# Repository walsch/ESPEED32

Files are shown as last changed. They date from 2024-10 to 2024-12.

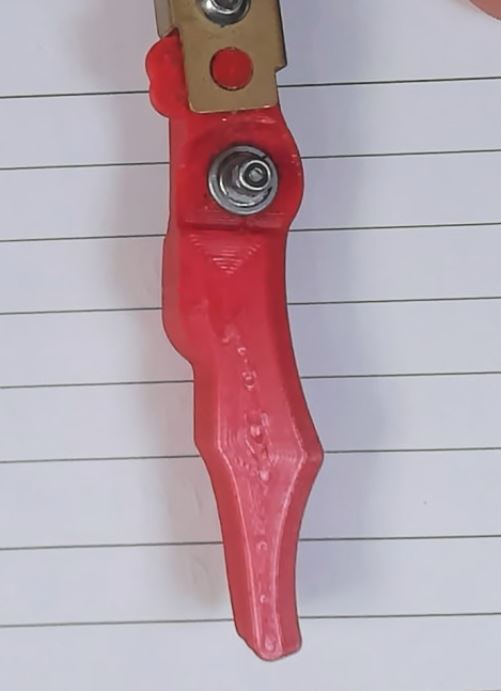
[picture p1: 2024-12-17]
Mechanical/longButton.JPG

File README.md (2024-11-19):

# SlotEsp32
WARNING: the magnetic sensor TLE493D-P3B6 A0 is the version 3 silicon and will be available on Digikey or mouser very likely in feb 2025
Cutting edge Slot car controller that has an ESP32 at its heart.
How to built it video:
https://github.com/MakerFabio/ESPEED32


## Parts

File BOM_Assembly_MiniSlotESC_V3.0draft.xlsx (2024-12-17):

Item | Function/position/note | Quantity per 1 remote | Available in stock: | have to buy to produce X pcs | Price per batch including shipping[euro] | purhcase Batch item count | Price per each item | Price per this item in the remote | Supplier | Last order link | Cost per remote Includes 3D prints (10 PCS lot) |  | Total Cost (including Cable and plug) |  | Want to produce (X pieces)
PCB + passive components |  | 1.00 | 8.00 | -2.00 | 60 | 10 | 6 | 6 | JLC PCB |  | 24.5 | Euro | 33.8 | Euro | 6
ESP32 devkit |  | 1.00 | 2.00 | 4.00 | 11.37 | 3 | 3.79 | 3.79 | Aliexpress | https://www.aliexpress.com/item/1005005972312714.html
Buzzer Passive 9032 |  | 1.00 | 6.00 | 0.00 | 4.24 | 5 | 0.848 | 0.848 | Aliexpress | https://www.aliexpress.com/item/1005004981491268.html
Encoder 15MM Plum handle |  | 1.00 | 6.00 | 0.00 | 3.29 | 5 | 0.658 | 0.658 | Aliexpress | https://www.aliexpress.com/item/1005001423863921.html?spm=a2g0o.cart.0.0.17b138da6YW7v5&mp=1
Knobs for rotary encoder | 15X17mm 6mm Shaft Hole AG2 | 1.00 | 12.00 | -6.00 | 1.9 | 25 | 0.076 | 0.076 | Aliexpress | https://www.aliexpress.com/item/1005005407773040.html
1.3" OLED Display Module White/Blue Color Drive Chip SH1106 128X64 (tenstar robot) |  | 1.00 | 6.00 | 0.00 | 5.46 | 2 | 2.73 | 2.73 | Aliexpress | https://www.aliexpress.com/item/1005005967766159.html
Electrolitic Cap 2200uF 16V | also 4700uF is OK, but needs to fit with wires inside the nhandle and not close too the PCB | 1.00 | 5.00 | 1.00 | 2.21 | 10 | 0.221 | 0.221
BTN9960LV | Motor Control | 1.00 | 4.00 | 2.00 | 27.7 | 10 | 2.77 | 2.77 | Digikey
IPD90P03P4L-04 | pCh mosfet | 1.00 | 7.00 | -1.00 | 16.2 | 10 | 1.62 | 1.62 | Digikey
TLE493D-P3B6 A0 ( v3 silic) | Magnetic sensor | 1.00 | 5.00 | 1.00 | 17.3 | 10 | 1.73 | 1.73 | Digikey (from feb 2025)
Thread insert M3, M3x5xOD4.4 100pcs | 4 for case closure 1 for PCB to case 1 for trigger to bearing 1 trigger tension | 7.00 | 50.00 | -8.00 | 5.79 | 100 | 0.0579 | 0.4053 | Aliexpress | https://www.aliexpress.com/item/1005005444256360.html
Screw M3x12mm button head | PCB fix to case & trigger tension(slide) | 2.00 | 29.00 | -17.00 | 2.48 | 50 | 0.0496 | 0.0992
Screw M3x10mm button head | Trigger to wahser to bearing | 1.00 | 10.00 | -4.00 | 2.48 | 50 | 0.0496 | 0.0496
Screw M3x20 flat head | Case closure display position | 3.00 | 50.00 | -32.00 | 2.48 | 50 | 0.0496 | 0.1488 | Aliexpress | https://www.aliexpress.com/item/1005006180128211.html
Screw M3x25 flat head | Case closure handle position | 1.00 | 35.00 | -29.00 | 2.69 | 25 | 0.1076 | 0.1076 | Aliexpress | ss.com/item/1005006180128211.html?spm=a2g0o.order_detail.order_detail_item.4.28ab582fOlswF8&gatewayAdapt=glo2ita
Screw M5x25mm buttn head | Trigger travel adjust | 1.00 | 4.00 | 2.00 | 2.9 | 10 | 0.29 | 0.29 | Aliexpress | https://www.aliexpress.com/item/32810852732.html
Spring Compression for trigger travel (0,6x7) | Trigger travel adjust | 1 | 6 | 0.00 | 3 | 10 | 0.3 | 0.3
Spring Extension for trigger tension (0,4x5x20mm) | Trigger Tension | 1.00 | 6.00 | 0.00 | 1.7 | 10 | 0.17 | 0.17
Ball Bearing | Trigger bearing | 1.00 | 5.00 | 1.00 | 2.52 | 10 | 0.252 | 0.252 | Aliexpress | https://it.aliexpress.com/item/32986140134.html
Magnet Diametrically Neodimium 5x2,5 mm | Tirgger Pos Sensor | 1.00 | 18.00 | -12.00 | 6.13 | 30 | 0.2043333333 | 0.2043333333 | Aliexpress
3DprintEnclosure(all parts including trigger and washers, quantity expressed in grams) |  | 81.00 |  |  | 25 | 1000 | 0.025 | 2.025 |  |  |  | Want to produce(X pcs)
Cable AWG 14 silicon | Yellow wiper, Red +, Black - | 3.00 | 15.00 | 3.00 | 5.55 | 5 | 1.11 | 3.33 |  |  |  | X pcs
Plug Magic |  | 1.00 | 15.00 | -9.00 | 6 | 1 | 6 | 6 | eBay

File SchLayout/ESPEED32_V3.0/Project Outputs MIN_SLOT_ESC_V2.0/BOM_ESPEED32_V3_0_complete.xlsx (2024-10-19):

Comment | Designator | Footprint
Comment | Designator | Footprint | JLCPCB Part #（optional） | JLC BASIC/EXTENDED | Mounting Option | Quantity | Description
NO_POP_Mill-Max 2501-2-00-80-00-00-07-0 | 5V | TEST POINT MILL-MAX 2501-2-00-80-00-00-07-0 |  |  | DO NOT MOUNT | 1 | testpad 1mm diameter
BUZ9032SMD | BUZ | BUZ9032_SMD |  | BuySeparately |  | 1 | Header, 2-Pin
100nF | C1, C6, C8, C9, C10, C11, C12 | C0603 | C28233 | BASIC |  | 7 | CAP / CERA / 100nF / 25V / 10% / X8R (EIA) / -55°C to 150°C / 0603(1608) / SMD / -
10nF 50V 0603 | C2, C4, C7, C13, C14 | C0603 | C57112 | BASIC |  | 5 | CAPACITOR, European symbol
22uF | C3, C15, C16 | CAPC3225X270N | C13585 | BASIC |  | 3 | CAP / CERA / 22uF / 25V / 20% / X5R (EIA) / -55°C to 85°C / 1210(3225) / SMD / -
1uF | C5 | CAPC1608X87N-1 | C15849 | BASIC |  | 1 | CAP / CERA / 1uF / 25V / 20% / X5R (EIA) / -55°C to 85°C / 0603(1608) / SMD / -
5016 | CAP-, CAP+, GND, VIN+, WIPER | CON-SMD-TP-5016 |  |  | DO NOT MOUNT | 5 | Test Point, Compact, Surface Mount, Finish- Silver Plate
RF05VYM2SFH | D2 | DIO-SMD-RF05VYM2SFH | C509964 |  |  | 1 | Super Fast Recovery Diode
ZENER 10V(MM3Z10VT1G) | DZ3 | SOD323 | C39057 |  |  | 1 | Zener 10V MM3Z10VST1G
PEC11L-4120K-S0020 | ENC1 | SW-THT-PEC11L-4XXXK-SXXXX |  |  | DO NOT MOUNT | 1 | 11 mm Low Profile Encoder
HTSW-103-07-G-S | EXT_MOT, T_POT | CON-THT-2.54-3-1-8.38 |  |  |  | 2 | Through hole .025 SQ Post Header, 2.54mm pitch, 3 pin, vertical, single row
IFX7805ABTF | G1 | TO228P998X235-3N-2-V | C897464 | Extended |  | 1 | Three Terminal 1.0A Positive Voltage Regulator
OLED128x64 MDOB128064V2V-YI | OLED1 | OLED 128X64 1.3" |  |  |  | 1 | Header, 4-Pin
2N7002WT1G | Q1 | SOT65P220X100-3N | C232391 | Extended |  | 1 | Insulated-Gate Field-Effect Transistor (IGFET), N-Channel, Enhancement, Body Diode, Resistor Gate, ESD Diode Gate/Source, Pin 1 Gate, 2 Source, 3 Drain, 3 Pins
IPD90P03P4L-04 | Q2 | TO228P998X235-3N-2-V |  |  |  | 1 | OptiMOS - P2 Power-Transistor, P-channel-Enhancement mode, VDS -30V
0R | R1, R16, R18, R19 | R0603 | C21189 | DOUBLE CHECK |  | 4 | General Purpose Chip Resistor
10k | R2, R9, R10, R11, R12, R13, R15 | R0603 | C25804 | BASIC |  | 7 | RES / STD / 10k / 100mW / 5% / 100ppm/K / -55°C to 155°C / 0603(1608) / SMD / -
2.2k | R3, R6, R7, R8, R14, R20, R21, R22, R23, R24 | R0603 | C4190 | BASIC |  | 10 | RES / STD / 2.2k / 100mW / 1% / 100ppm/K / -55°C to 155°C / 0603(1608) / SMD / -
N.M. 0R | R4, R5 | R0603 |  |  |  | 2 | General Purpose Chip Resistor
PTS645SM43SMTR92 LFS | S1 | SW-SMD-PTS645SK43SMTR92 | C285473 |  |  | 1 | Tact Switches, Variety of Actuator Lengths
HTSW-104-07-G-S | SPARE | HDRV4W64P254_1X4_1016X248X838B |  |  | DO NOT MOUNT | 1 | Through hole .025 SQ Post Header, Hi-Temp Strip, 2.54mm pitch, 4 pin, vertical, single row
ESP32-DEVKIT-V1 | U1 | MODULE_ESP32_DEVKIT_V1 |  |  |  | 1 | Dual core, Wi-Fi: 2.4 GHz up to 150 Mbits/s,BLE (Bluetooth Low Energy) and legacy Bluetooth, 32 bits, Up to 240 MHz
BTN9960LV | U2 | IFX-PG-HSOF-7-1-V |  |  |  | 1 | MOTIX Single Half-Bridge with Integrated Driver IC
TLE493D-W2B6 A3 | U3 | SOP95P280X110-6N-V |  |  |  | 1 | Low Power 3D Hall Sensor with I2C Interface and Wake Up Function, Temp Range(-40 to 125°C)
LEGENDA:(colour code)
Not mounted but Nice to havefrom digik | Extended of Basic | NOT needed /not mounted |  |  |  | I will mount later by myself

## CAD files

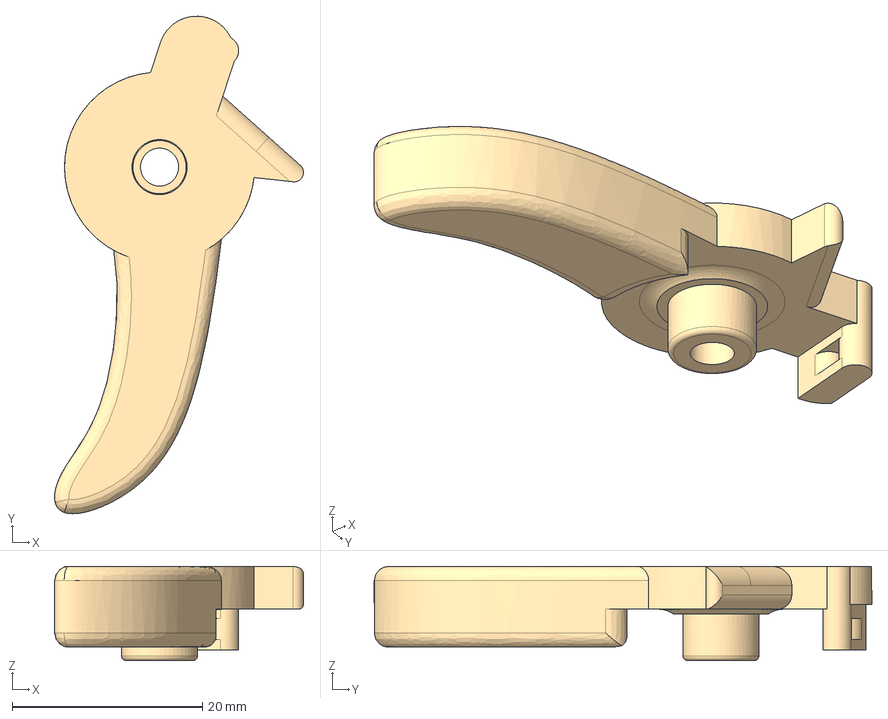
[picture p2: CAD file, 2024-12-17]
Mechanical/TrigV3.2Tick_V29.step
26.2 x 52.3 x 9.90 mm

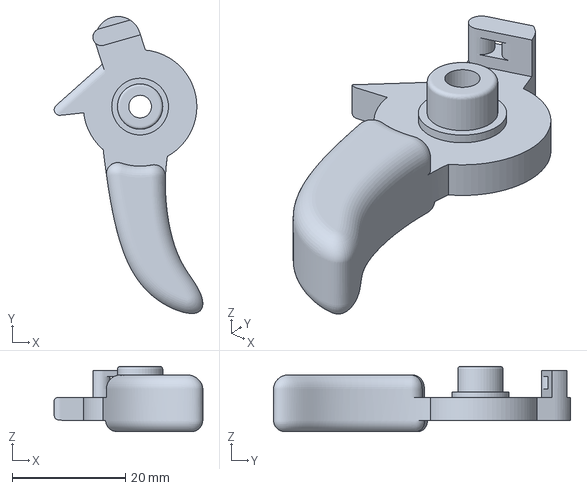
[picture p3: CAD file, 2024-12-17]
Mechanical/3Dprint/TrigThickV3_24.3mf
26.2 x 52.3 x 11.5 mm

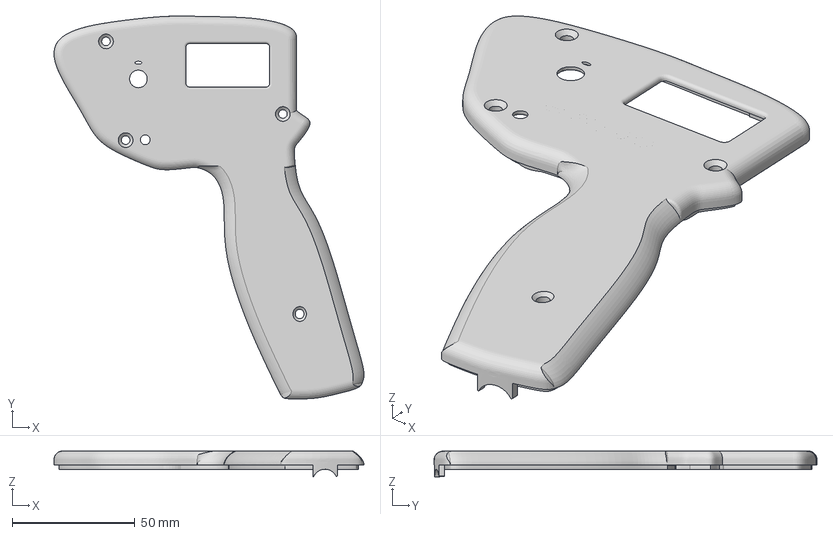
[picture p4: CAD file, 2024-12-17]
Mechanical/3Dprint/HandleTopTextV39.3mf
126.1 x 155.8 x 10.6 mm

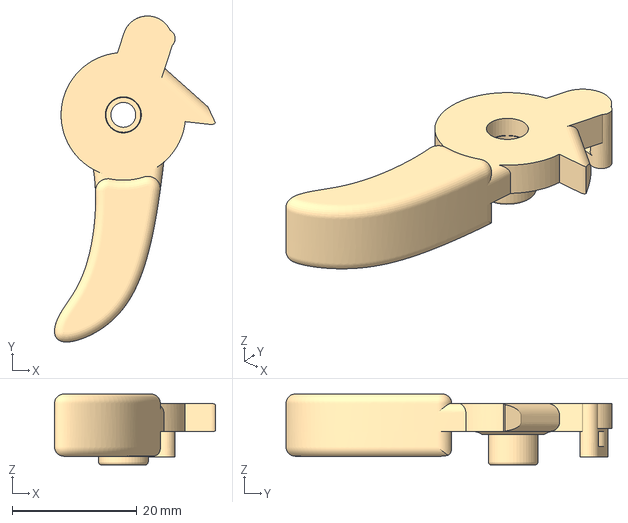
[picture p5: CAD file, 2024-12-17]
Mechanical/3Dprint/TrigVeryThick10mm.3mf
25.9 x 52.3 x 11.4 mm

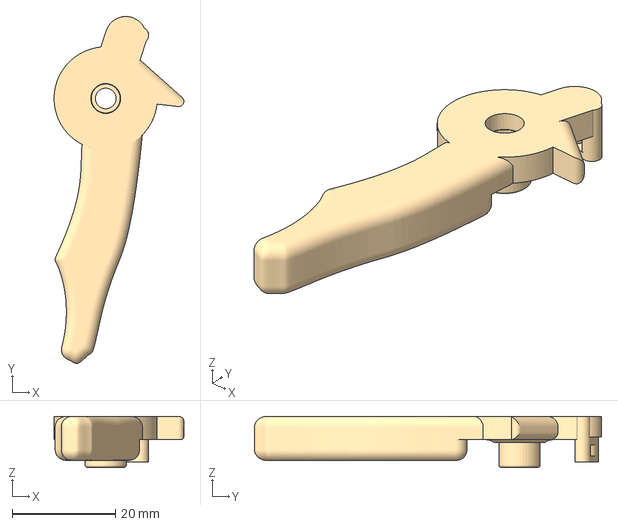
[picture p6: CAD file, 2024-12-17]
Mechanical/3Dprint/TrigLongV33.3mf
25.1 x 67.2 x 9.90 mm

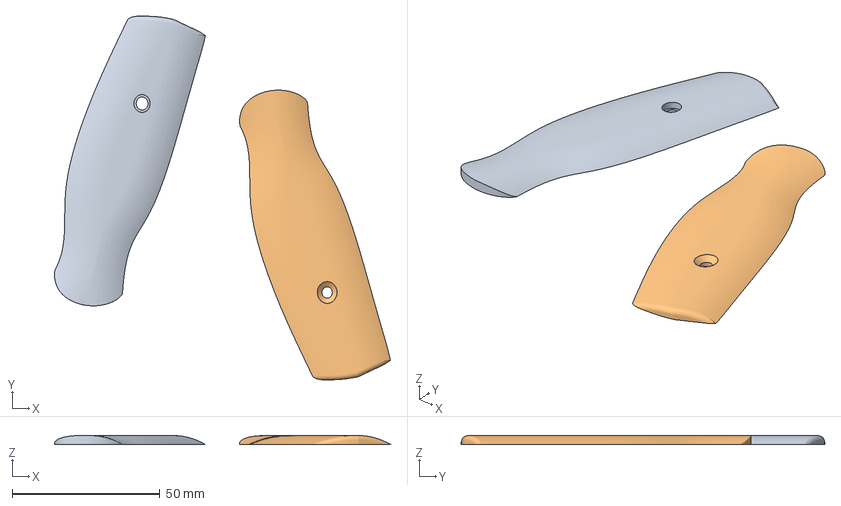
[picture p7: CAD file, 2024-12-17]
Mechanical/3Dprint/RoundingBot.3mf
113.8 x 123.3 x 3.00 mm
RoundingBot
RoundingTop

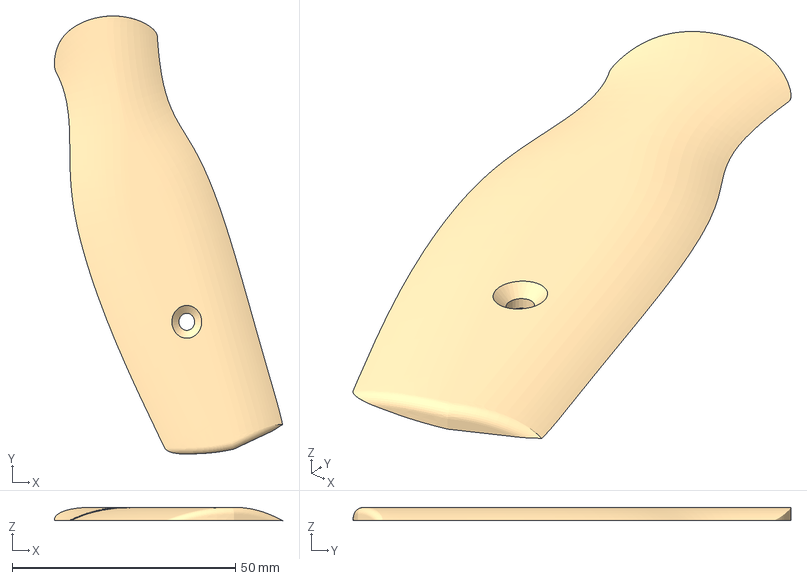
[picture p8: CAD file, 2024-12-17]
Mechanical/3Dprint/RoundingTop.3mf
51.1 x 98.2 x 3.00 mm

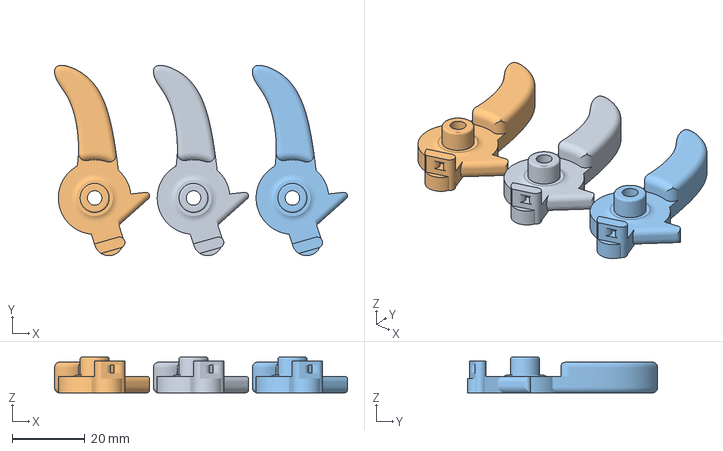
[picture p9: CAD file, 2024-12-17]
Mechanical/3Dprint/TrigV32thick.3mf
80.6 x 52.3 x 9.90 mm
TrigV3_1 x 3

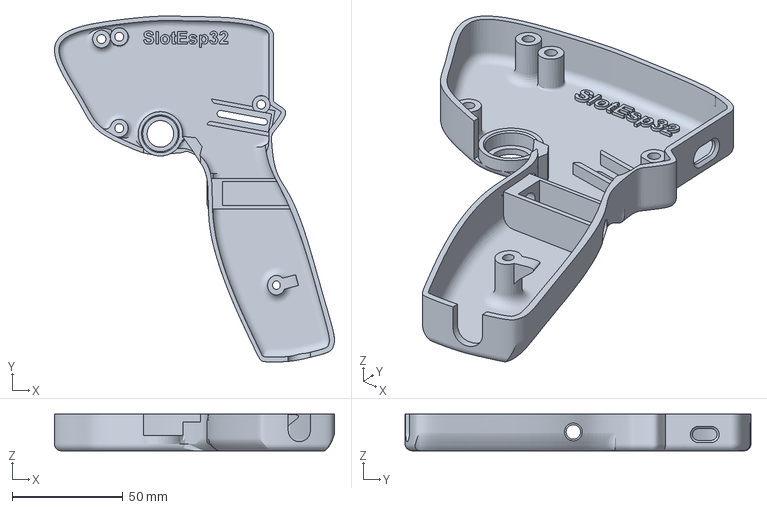
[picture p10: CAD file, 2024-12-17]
Mechanical/3Dprint/HandleBot_V20.3mf
126.1 x 155.8 x 16.5 mm

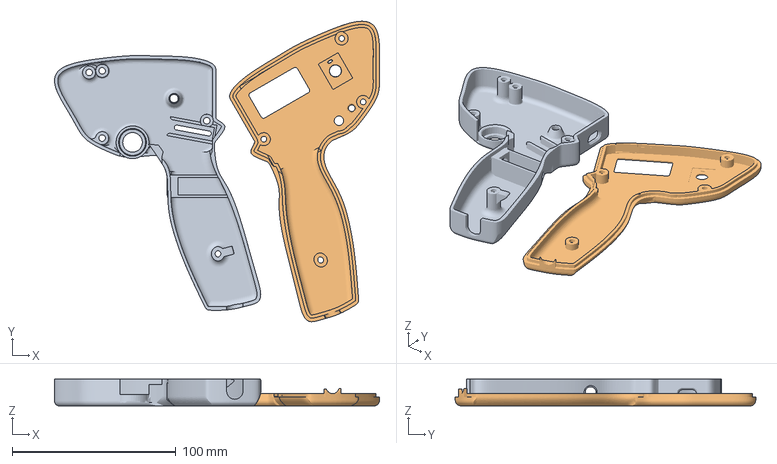
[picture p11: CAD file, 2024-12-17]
Mechanical/3Dprint/HandleBotTextV37.3mf
198.8 x 183.8 x 16.5 mm
HandleBot (1)
HandleTop

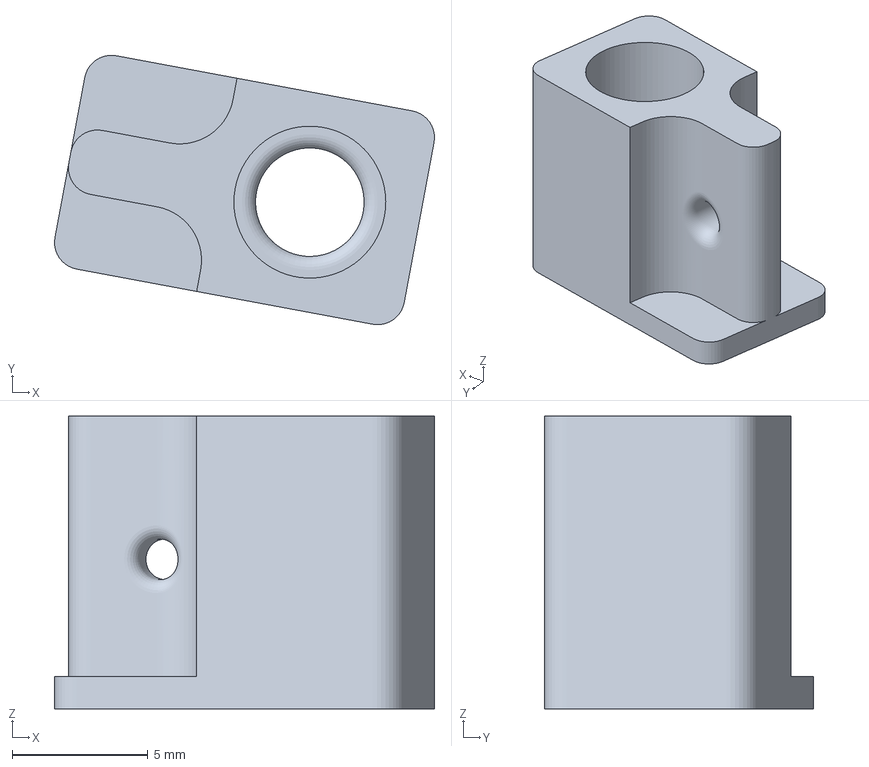
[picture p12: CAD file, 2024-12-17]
Mechanical/3Dprint/Slide.3mf
14.0 x 9.93 x 10.8 mm

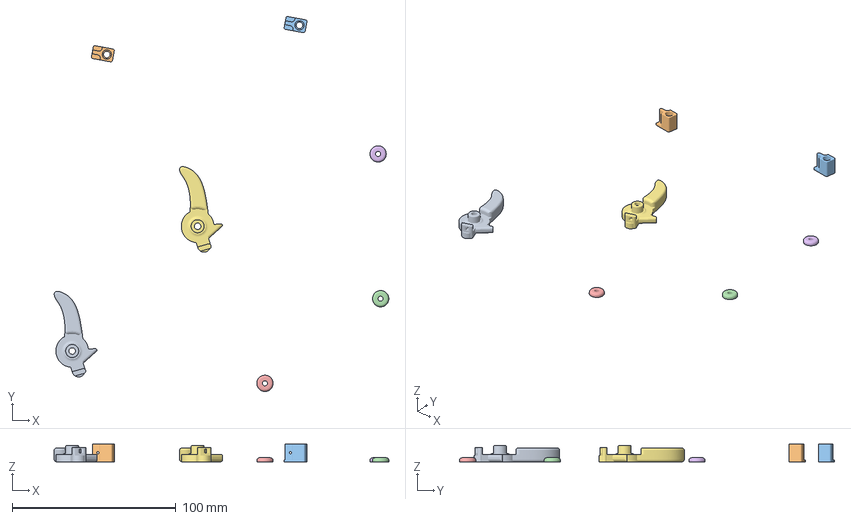
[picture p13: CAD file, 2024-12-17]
Mechanical/3Dprint/TrigV3_29.3mf
204.7 x 229.3 x 10.8 mm
TrigV3_1 x 2
Washer x 3

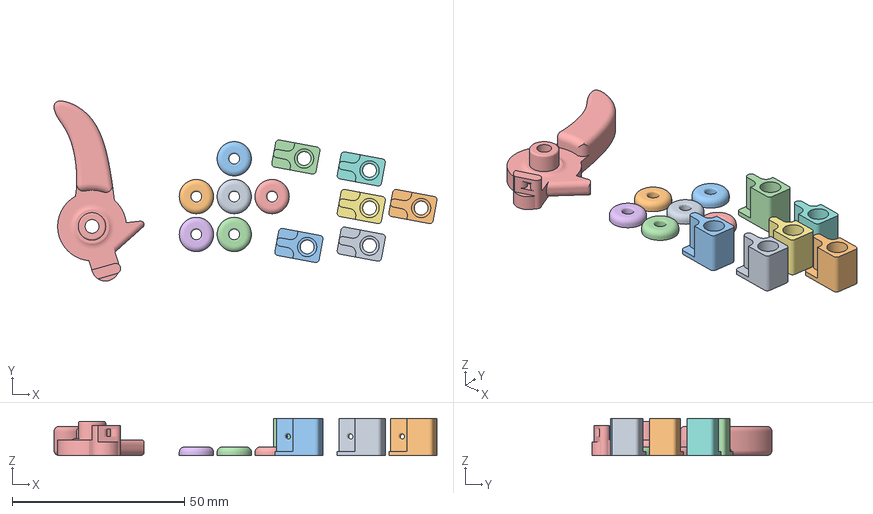
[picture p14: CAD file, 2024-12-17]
Mechanical/3Dprint/5Washer5slides1trig.3mf
111.3 x 52.3 x 10.8 mm
Washer x 6
TrigV3_1

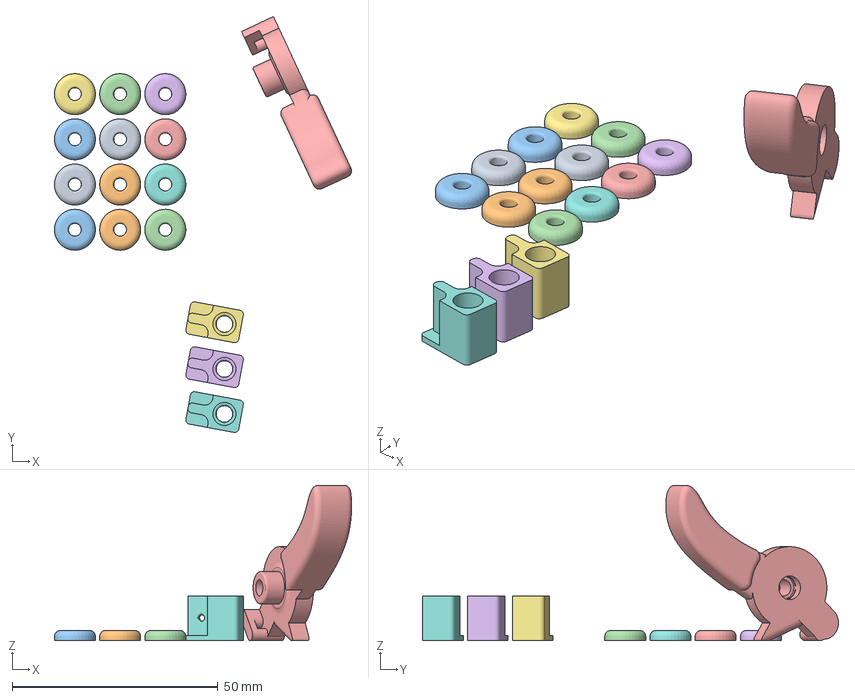
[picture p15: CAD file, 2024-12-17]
Mechanical/3Dprint/WasherOnly.3mf
72.3 x 101.2 x 37.8 mm
Washer x 12
TrigV3_1

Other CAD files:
Mechanical/3Dprint/tappo.3mf
Mechanical/3Dprint/TrigMidV33.3mf
Mechanical/3Dprint/HandleTopV19.3mf
Mechanical/3Dprint/Body1.3mf

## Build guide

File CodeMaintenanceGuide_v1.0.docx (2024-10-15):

# ESPEED32 Slot Car Electronic Speed Controller

Code Maintenance Guide

EN

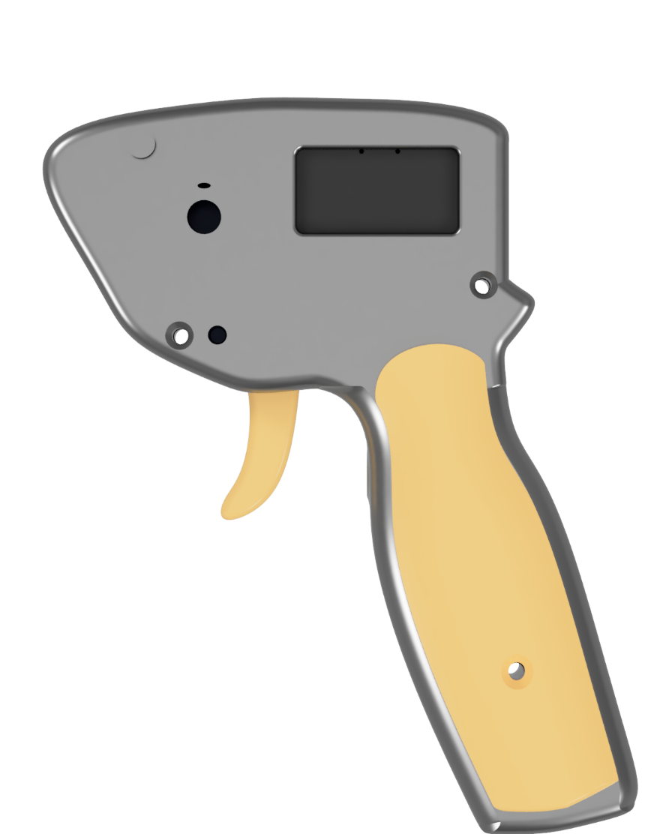
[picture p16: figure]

# 1 About this document

The goal of this document is to provide detailed information on how the code for the ESPEED32 Slot Car Electronic Speed Controller works, in order to ensure the possibility of future upgrades. This includes high level flow charts as well as low level implementation details.

This documents also includes hints at coding styles that must be maintained in order to obtain a clean, readable and understandable code.

Any changes to the code high-level structure or concept shall be documented here, as well as the rationale behind every change.

# 2 Coding style and good practices

A good and coherent coding style allows the code to be easily understandable even to new programmers, ensuring the possibility to be maintained and upgraded in the future.

No more “I don’t know what this function does, but if we remove it, it stops working”.

It’s important that the standards that are defined in this chapter are meticulously followed.

## 2.1 Naming

### Variables

The name of a variable should immediately convey functional relevant meaning. The name should also be made of fully formed, plain English words, rather than abbreviations that serve no purpose other than making the name harder to read:

uint16_t selectedOption;

uint16_t retValue;

uint16_t throttleSetpoint; /* Understandable English words */

Example 2.1 Good variable naming examples

uint16_t xyz;

uint16_t tmp;

uint16_t throtStp; /* Unintelligible abbreviations */

Example 2.2 Bad variable naming examples

To obtain a readable and coherent code, it’s important that a case style is chosen and followed throughout all the code. The proposed style is the following:

uint16_t localVariable; /* camelCase for variables, starting with a lower case */

#define CONSTANT_MACRO /* SNAKE_CASE with all upper case letters for MACROS */

Example 2.3 Case style for variables and macros

Another good practice is to add a g_ prefix in front of global variables, so that they can be identified immediately when looking at the code, while also preventing variable shadowing (local-scope variable with the same name of a global variable):

uint16_t g_globalVariable; /* g_ prefix for global variables */

Example 2.4 Global variables style

Finally, it might be useful to keep track of the measurement unit in the variable itself, especially when the measurement unit must be considered when the variable is used, or when there are similar variable expressed in different units. This is done by adding a suffux _<unit>. When naming variables that store current or previous values, use the prefix curr or prev, respectively.

uint16_t actualTrigger_raw;

uint16_t deadBand_pct;

uint16_t deltaTime_uS;

Example 2.5 Good variable naming includes measurement units

### Functions

The guidelines for naming functions are the same as for naming variables:

- Meaningful names;
- Coherent style (camelCase);
- Using fully formed words rather than useless abbreviations.

The naming of the functions should also be consistent in the form of verbNoun or actionNoun style:

void showWelcomeScreen();

void initMenuItems();

uint16_t addDeadBand();

Example 2.6 Good function naming examples

void displayInit(); /* wrong order (nounVerb), should be verbNoun */

void calcThrot(); /* Useless abbreviations make the name unintelligible */

uint16_t init_Encoder(); /* wrong case style, should be camelCase */

Example 2.7 Bad function naming examples

### Typedefs

The naming conventions for enum and structs shall follow the same guidelines stated above, with the exception for the casing style, which shall be CamelCase, starting with an upper case letter (as opposed to variables, whose style is camelCase starting with a lower case letter). A suffix _enum and _type shall be added respectively to enumerations and structs:

typedef struct {

unit16_t inputThrottle;

unit16_t outputSpeed;

} ThrottleCurveSetpoint_type;

typedef enum {

ITEM_SELECTION,

VALUE_SELECTION

} MenuState_enum;

Example 2.8 Typedefs naming examples

## 2.2 Comments

A good code is a commented code!

### Line comments

A portion of a code should never leave you wondering what the intent of the original programmer was: comments should follow every non-obvious statement and describe what it is doing.

Additionally, variables, struct members and macro should also be commented.

Line comments should be placed in the same line of the statement that they are describing, and should not be too long (continue the comment in the line below if needed).

Multiple adjacent line comments should be aligned, whenever it’s possible

Line comments shall start with /* and end with */. Double slash comments (//) are not allowed!

uint16_t carSelected; /* index of the currently selected car */

unit16_t encoderMainSelector; /* this comment is aligned to the previous ones

If the comment is too long, continue it to a new line, but keep the commments aligned! */

unit16_t deltaValue = abs(maxValue – minValue); /* Calculate the difference between max and min value */

Example 2.9 Good line comments examples

### Function comments

Every function body shall be commented as to include:

- What it does in detail
- Important remarks on the implementation
- For every argument (parameter): what it is, and in what measurement unit is expected to be
- What value it returns, in what measurement unit

The comment should follow the doxyge’s format, as shown below:

/**

* Saturate an input value between an upper and lower bound

*

* @param paramValue The input value to be saturated

* @param minValue The lower bound

* @param maxValue The upper bound

* @return The saturated input value.

*/

uint16_t saturateParamValue(uint16_t paramValue, uint16_t minValue, uint16_t maxValue)

{

/* Function does something here… */

}

Example 2.10 Good function comment example

## 2.3 Other good practices

The following guidelines should be followed, in order to obtain a clean, readable and coherent code.

### Curly bracket placements { }

Curly bracket shall be opened in a new line, rather than on the same line.

It’s also a good practice to put a [space] after keyword statements (if, for, while, etc…).

if (condition)

{

/* if true do something… */

}

else

{

/* Do something else… */

}

Example 2.11 Correct curly bracket placement

Opening a curly bracket in the same line makes the code more difficult to read. Also, even if single line statements don’t require to be placed within curly bracket, it’s important to use them, for the sake of readability

if (condition) {

/* if true do something… */

}

if (condition)

return;

Example 2.12 Wrong curly bracket placement

### Mathematical statements

To make statement more readable and understandable, apply the following guidelines:

- Try to fit all the operations in one single statement, if possible;
- Put a [space] in between operators and operands;
- Use parenthesis to make the math clear!
- Avoid magic numbers, use constants definitions

inputThrottle_pct = (inputThrottle * 100) / THROTTLE_NORMALIZED; /* TakeinputThrottle (from 0 to THROTTLE NORMALIZED) and convert it to a 0% to 100% value */

counter ++; /* Increase counter */

Example 2.13 Correct math statements style

inputThrottle_pct = inputThrottle*100/255; /* No space between operators.

No parenthesis, it’s unclear what is the order of the operations.

Magic numbers */

Example 2.14 Wrong math statements style

## 2.4 Versioning

Keep versioning updated within the code. This allows to compare software versions

The following lines (13, 14 and 15 of the main .ino file) must be kept updated.

#define SW_MAJOR_VERSION 1

#define SW_MINOR_VERSION 99

/* Last modified: 15/10/2024 */

Figure 2.1 Versioning code lines

In particular, the SW_MAJOR_VERSION and SW_MINOR_VERSION macro are also used by the code to verify during the initialization what version of the code is currently flashed in the device.

If the versions don’t match, the EEPROM memory is erased. Keep updated the version numbers, especially if there was a change in the structure of the EEPROM stored variables!

# 3 Code structure

The code of the ESPEED32 is structured, as most microcontrollers, in two parts: Setup and Loop; in the case of the ESPEED32 the Loop part is replaced by two parallel Tasks, that run side by side on two different Cores.

The Setup simply consist of setting up the hardware pins and initializing the essential hardware components such as the magnetic trigger sensor and the motor controller; other non-essential components (such as the OLED display and rotary encoder) are initialized later, in order to reduce the start-up time.

After the Setup, two separate Tasks are defined and pinned to two different Cores.

Task 1 is the low priority task and is pinned to Core 0. This task takes care of managing the OLED display, which includes elaborating the user input (by means of the rotary encoder) to navigate the menu and change the values of the parameters, while also displaying important telemetry data to the user.

Task 2 is the high priority task and is pinned to Core 1. This task takes care of periodically (every 0.5 ms) reading the trigger position and processing it (throttle-to-speed pipeline), and correctly setting the PWM output of the motor controller.

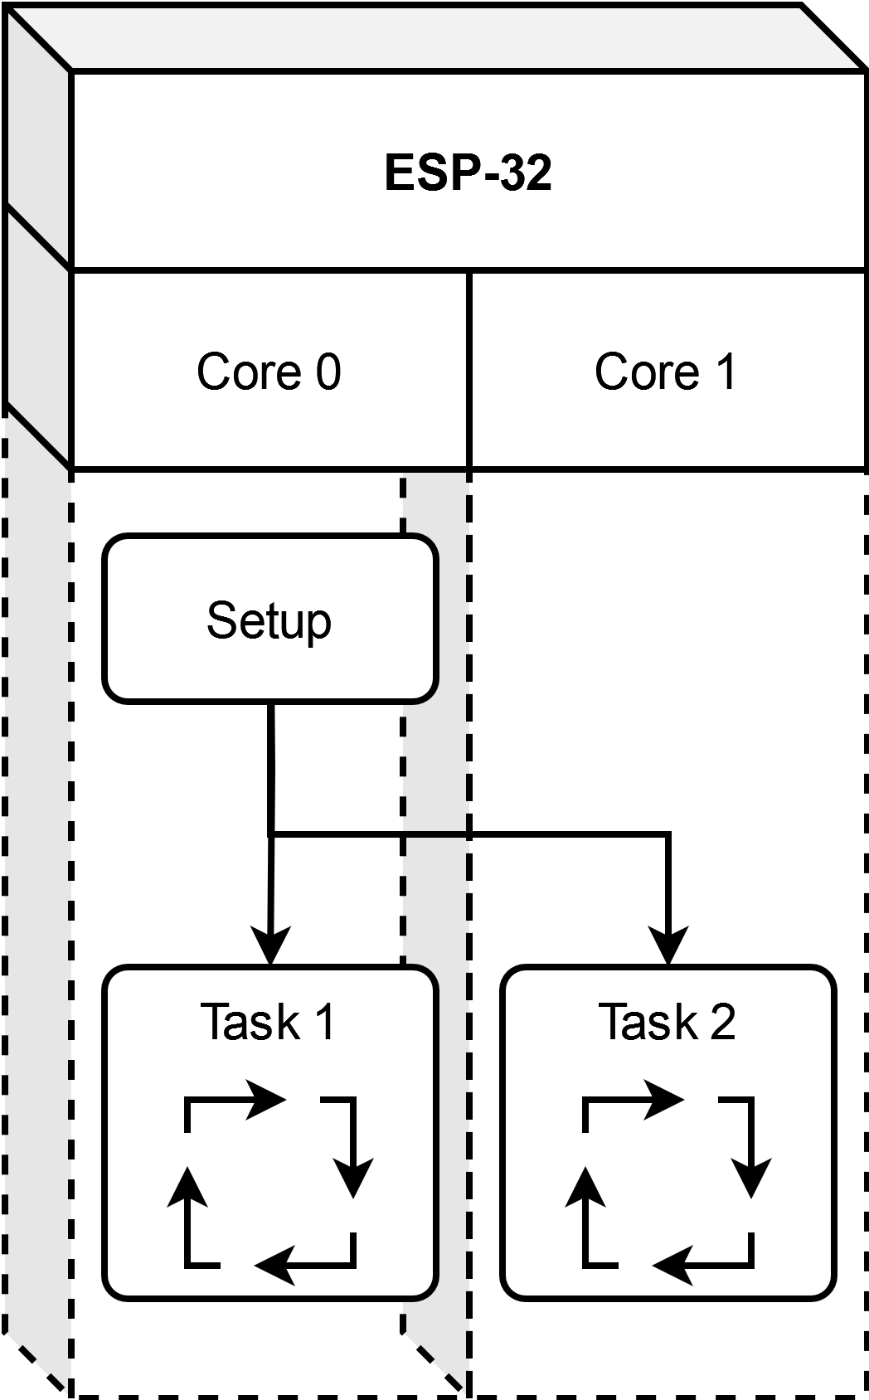
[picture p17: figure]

Figure 3.1 High-level structure of the main code

The implementation details of the two tasks are discussed in the sections below.

## 3.1 Task 1

Task 1 is the lower priority task, that takes care of managing the OLED display. It manages the encoder inputs to allow the user to navigate the menu, select the items and change their value.

The Task 1 code is structured as a Finite State Machine with four states:

- INIT, where the EEPROM stored variables are checked. If they are okay, the machine transitions to the WELCOME state. If the stored variables are outdated or not present, the machine transitions to the CALIBRATION state. It’s also possible, for the user, to manually go to the CALIBRATION state by keeping pressed the encoder button during the power-on.
- CALIBRATION, where the user is asked to fully press and release the trigger, in order to save the maximum and minimum readings of the trigger sensor. Then the machine transitions to the WELCOME state.
- WELCOME, where a simple welcome screen is shown for 1 second, before transitioning to the RUNNING state.
- RUNNING, where the main menu is shown. The machine remains in this state, and the only way to transition is to power-off the device. This is the state where the encoder inputs are taken to navigate the menu, select the parameters and change their value.

There is an additional fifth state, which is the FAULT. At the current implementation, this state is empty and unreachable, but there might be an use for it in the future.

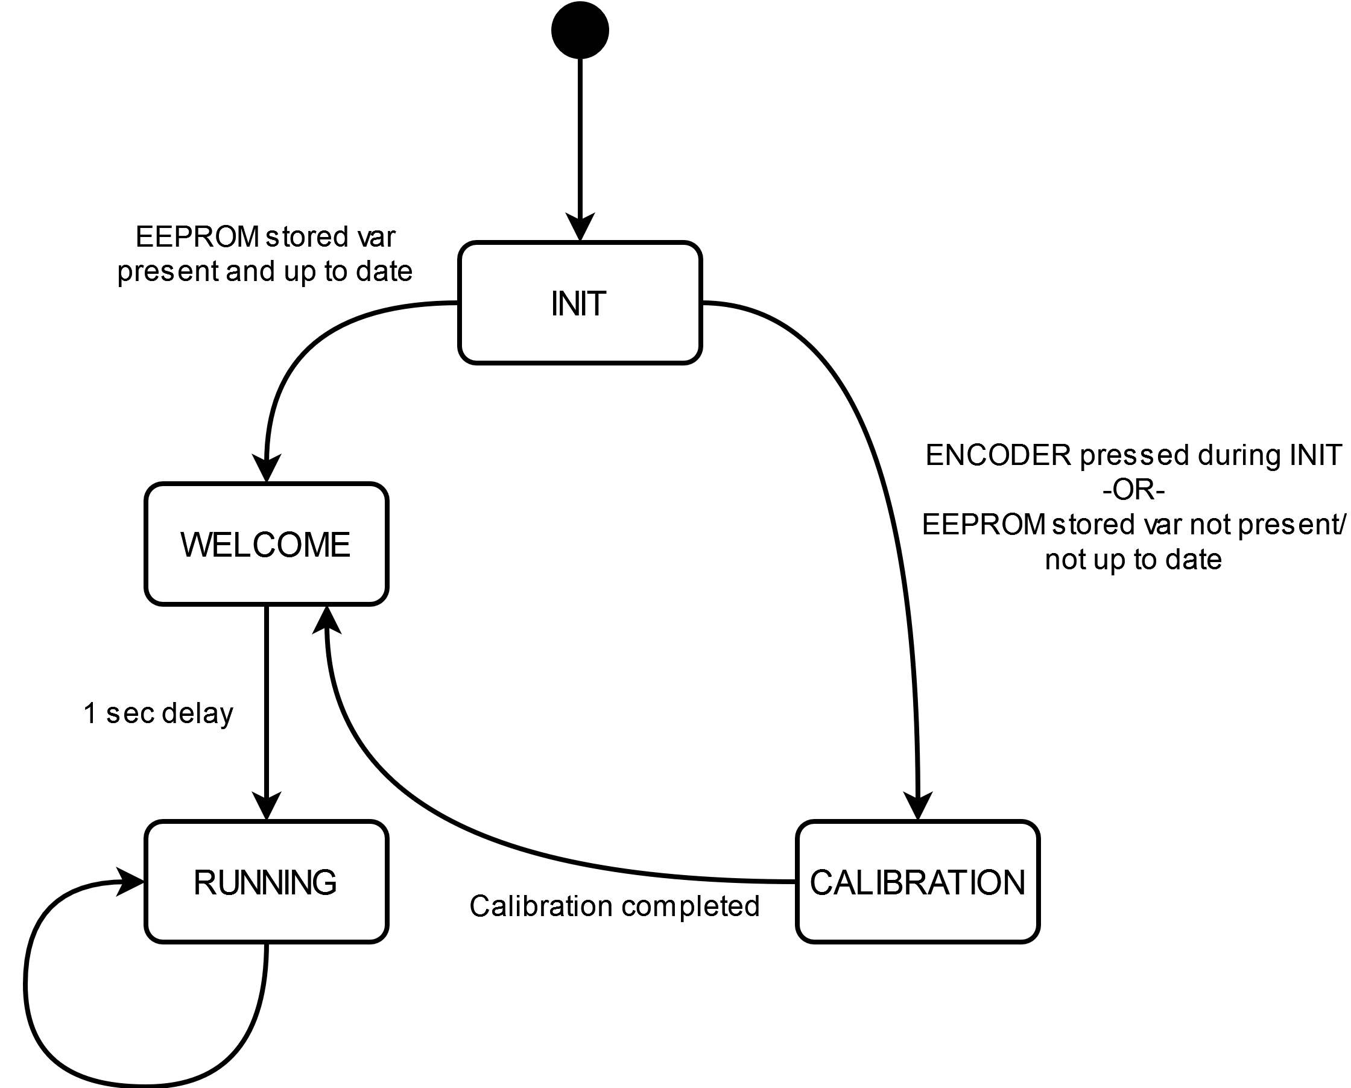
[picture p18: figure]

### Menu state

Figure 3.2 Task 1 state machine

While in the RUNNING state, the OLED display will show the main menu. The menu is a list of different items, followed by their value. The main menu will also behave as a state machine, with two possible state:

- ITEM_SELECTION: this is the starting state, where scrolling the encoder will scroll the items in the menu. Only one item is highlighted (this is the selected item), and rotating the encoder will change the selected item. Upon pressing the encoder, the menu state will switch to VALUE_SELECTION.
- VALUE_SELECTION: in this state, the selected item’s value will also be highlighted. Rotating the encoder now, will change the value of the selected item. Upon pressing the encoder button again, the new value will be saved in the EEPROM, and the menu will transition back to the ITEM_SELECTION state.

There also are special items, that upon selected will invoke a special callback. Once the callback returns, the menu will stay in the ITEM_SELECTION state.

This menu state machine is handled in the rotary_oButtonClick function, which is called at the beginning of the RUNNING state, if the encoder button has been clicked.

When transitioning from the ITEM_SELECTION to the VALUE_SELECTION menu state, the global variable g_encoderSelectedValuePtr is set to point to the variable that stores the actual value of the selected item (e.g., when BRAKE is highlighted, pressing the encoder button will set g_encoderSelectedValuePtr to point to g_storedVar.carParam[g_carSel].brake). Now, in the VALUE_SELECTION menu state, rotating the encoder will increase and decrease the value of the actual variable, through the pointer.

### Menu and Menu items

The Menu_type and MenuItem_type structs were created to have a modular design for a scrollable menu, that allows to quickly and easily add items.

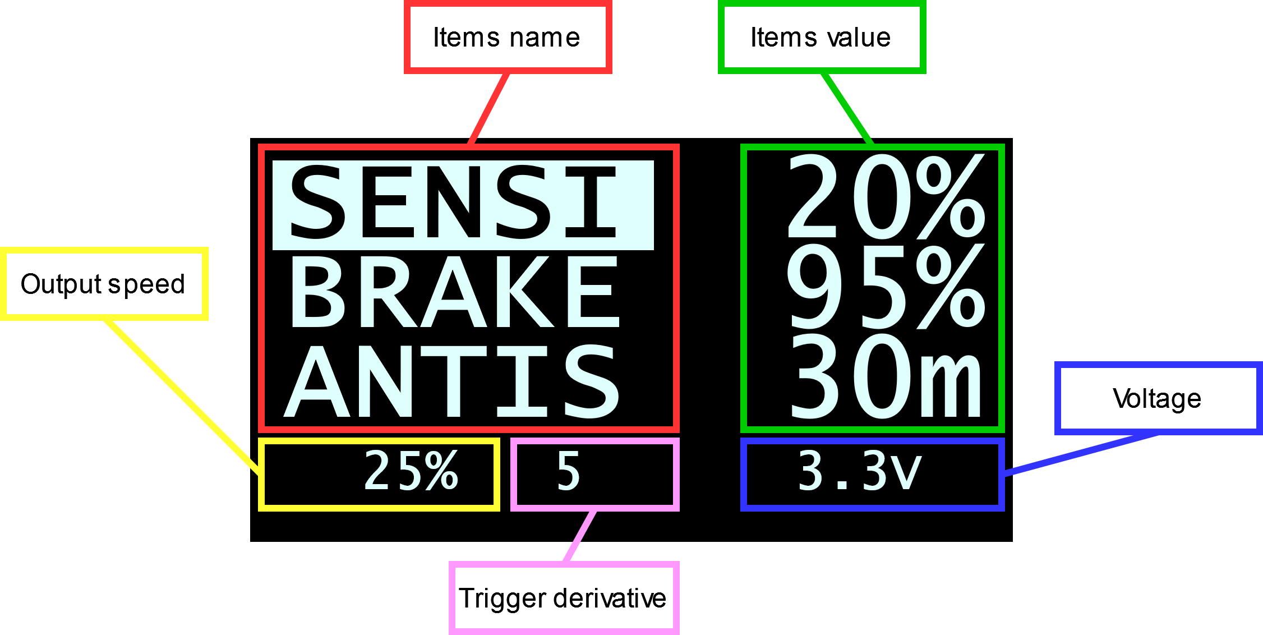
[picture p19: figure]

The menu and its items are only “graphical” elements, and they don’t actually store any parameter.

Figure 3.3 OLED display showing the main menu on the ITEM_SELECTION state.

It’s easy to think as a menu as a series of items that are displayed on the screen, along with their value. The Menu_type struct contains only two members: the uint16_t lines, which indicates how many items are displayed at a time, and an array of MenuItem_type, which are the actual items.

The MenuItem_type was designed to be as modular as possible. It describes an item in a menu.

It contains an array of char to store the name of the item: that is the name that is displayed on the menu (e.g., “SENSI”, “BRAKE”, “CURVE”, etc…).

It contains a pointer to a value: this is done so that the actual value is stored in other global variables. The value could be a number (e.g., SENSI, BRAKE, CURVE, etc…) or it could be a string (e.g., the CAR item value is the name of the selected CAR). An item can also not contain a value. The contents of the pointer (address of the variable that store the actual value) is passed to g_encoderSelectedValuePtr when the item is selected, as explained in Menu state.

The item also contains the upper and lower boundaries for the actual value, that are used to set the encoder boundaries in rotary_oButtonClick.

Finally, an item can contain a callback, that is a pointer to a function that shall be execute when the item is selected and the encoder button is pressed.

Table 1 Details of the MenuItem_type struct

Member | Type | Description
name | char[] | The name of the item, as it will be displayed on the menu, stored in an array of char.
value | void * | Pointer to the variable that contains the value of the item, stored as a generic void pointer. This is done so that it can print to different type of variables. When assigning this value, it must be cast to (void *) Value = (void *)&g_storedVar.carParam[g_carSel].brake; If the item doesn’t contain any value, this must be set to ITEM_NO_VALUE.
type | ItemValueType_enum | Indicates which type of variable address is stored in value. Possible enumerations are - VALUE_TYPE_INTEGER: value points to a uint16_t variable (must be 3 digits) - VALUE_TYPE_DECIMAL: value points to a uint16_t variable, but it will be printed as a decimal value (see decimalPoint). - VALUE_TYPE_STRING: value points to an array of chars.
maxValue | uint16_t | The maximum integer value that can be assigned to the actual variable. Only applies if type is VALUE_TYPE_INTEGER or VALUE_TYPE_DECIMAL.
minValue | uint16_t | The minimum integer value that can be assigned to the actual variable. Only applies if type is VALUE_TYPE_INTEGER or VALUE_TYPE_DECIMAL.
unit | char | A single characted that represents the measurement units of the value, which will be printed next to the value in the menu.

decimalPoint

uint8_t

In case type is set to VALUE_TYPE_DECIMAL, this indicates where the decimal point is placed. Possible values are 1 (decimal point is placed between right-most digit and middle digit) or 2 (decimal point is placed between left-most digit and middle digit). The variable holding the actual value must store an integer value (it’s up to the application to convert it when it’s used).

e.g.: PWM freq is a value that we want represented in kHz, ranging from 0.2 to 5.0. We are gonna create the menu item type with the following fields:

type: VALUE_TYPE_DECIMAL;

maxValue: 50;

minValue: 2;

decimalPoint: 1

Meaning that internally the values ranges from 2 to 50. When selected with the encoder in the main menu the value can be increased 1 by 1. The value that is displayed will be divided by 10^decimalPoint, to show values that ranges from 0.2 to 5.0. The application must take into account that the stored value will range from 2 to 50 during the calculations.
callback | FunctionPointer_type | The address of a function with no arguments that returns void, that will be invoked when the item is selected (e.g., CURVE item has callback = &showCurveSelection). If no callback, this should be set to ITEM_NO_CALLBACK

### Printing the menu

The code does not have a standard function to print the menu, since the Menu_type struct is used both for the main menu and the select car menu, which have different necessities; however, the same “Frame” approach is used.

A Frame is delimited by two numbers, a lower bound and an upper bound. The difference between the upper and lower bound is fixed to be the value of Menu_type.lines. Only the menu items within the Frame are displayed on screen. Scrolling the encoder allows to select the item displayed on screen. If the value of the encoder crosses the boundaries of the Frame, the Frame is shifted, so that the value of the encoder is within the Frame.

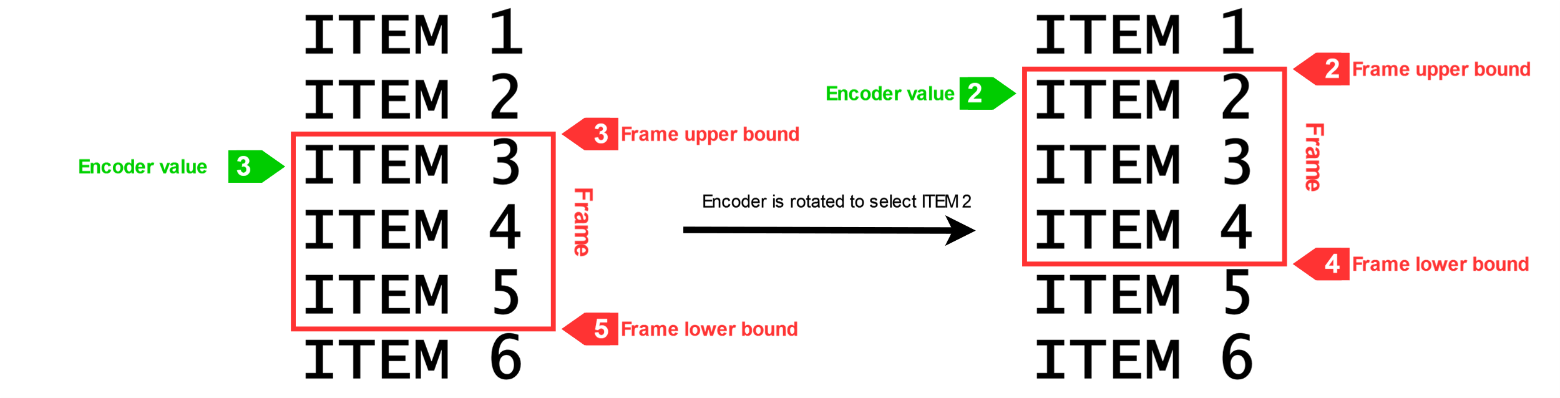
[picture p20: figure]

The items and their value are printed in a for loop for (uint8_t i = 0; i < menu.lines; i++) where they are addressed as menu.item[frameUpper + i]. It’s important that the encoder boundaries match the item array size.

Figure 3.4 Frame explanation.

## 3.2 Task 2

Task 2 is the high priority task, that takes care of calculating the correct speed output (duty cycle) depending on the user parameters and trigger position.

The task code is executed every 0.5 ms (500 µs), in order to provide a timely and smooth response to the trigger.

The code of Task 2 can be divided into three parts:

- Read Trigger position (input)
- Throttle-to-speed pipeline (elaboration)
- Set PWM (output)

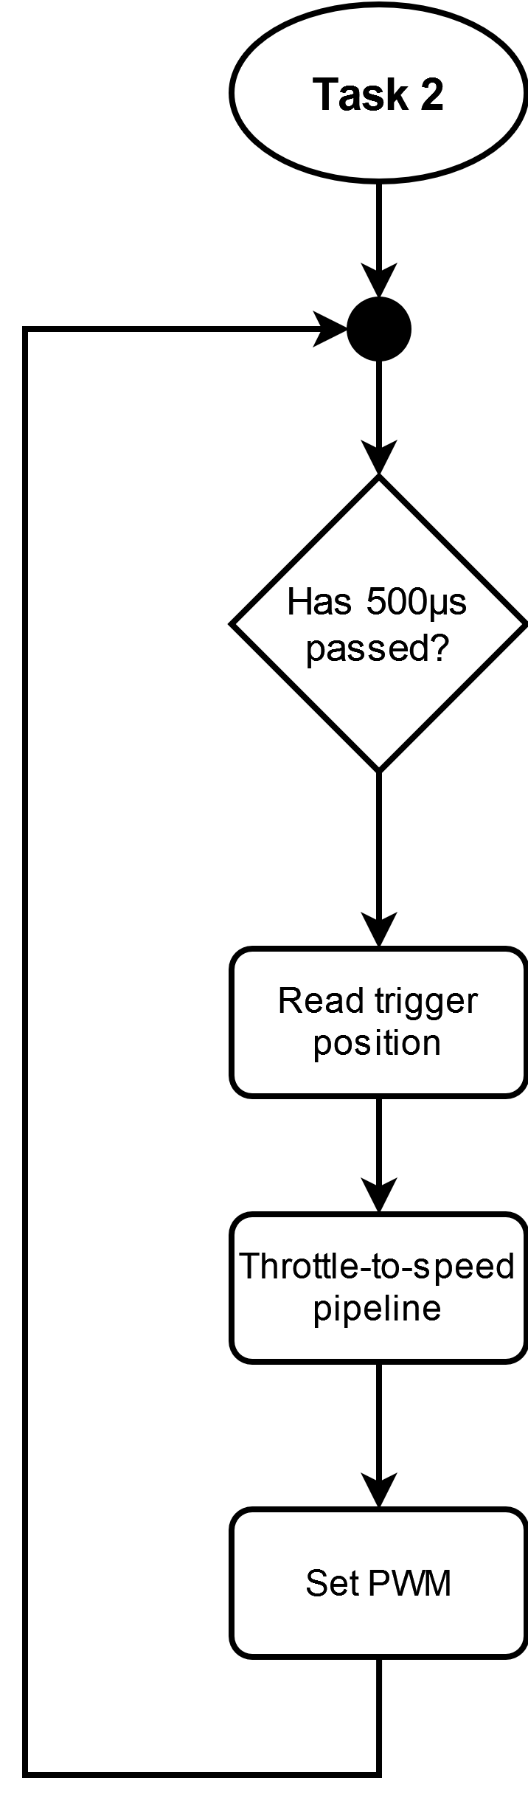
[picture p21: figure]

### Trigger reading

Figure 3.5 Task 2 flow chart

The trigger position is read at the beginning of the periodic Task, by calling the HAL_ReadTriggerRaw() function; this produces a raw value. The current raw trigger reading and the previous one (kept from the previous execution) are summed and divided by two, then stored in the escVar.trigger_raw variable.

### Throttle-to-speed pipeline

This part of the Task takes the trigger_raw input and elaborates it to produce a speed output. The pipeline is composed of different elaborations, which are described below.

#### Normalization

The raw input is taken, constraint between the maximum and minimum calibration values of the sensor, then re-scaled in the range 0 to THROTTLE_NORMALIZED (defined to be 256), which has a higher granularity with respect to the typical 0-100 range. This passage produces a normalized value.

#### DeadBand

A 3% deadband is added to the trigger_raw, to increase stability at full-pressed and full-released trigger positions. This elaboration sets to 0 every input that’s lesser than 3% of normalized range, and sets to THROTTLE_NORMALIZED every value that’s higher than 97% of the range.

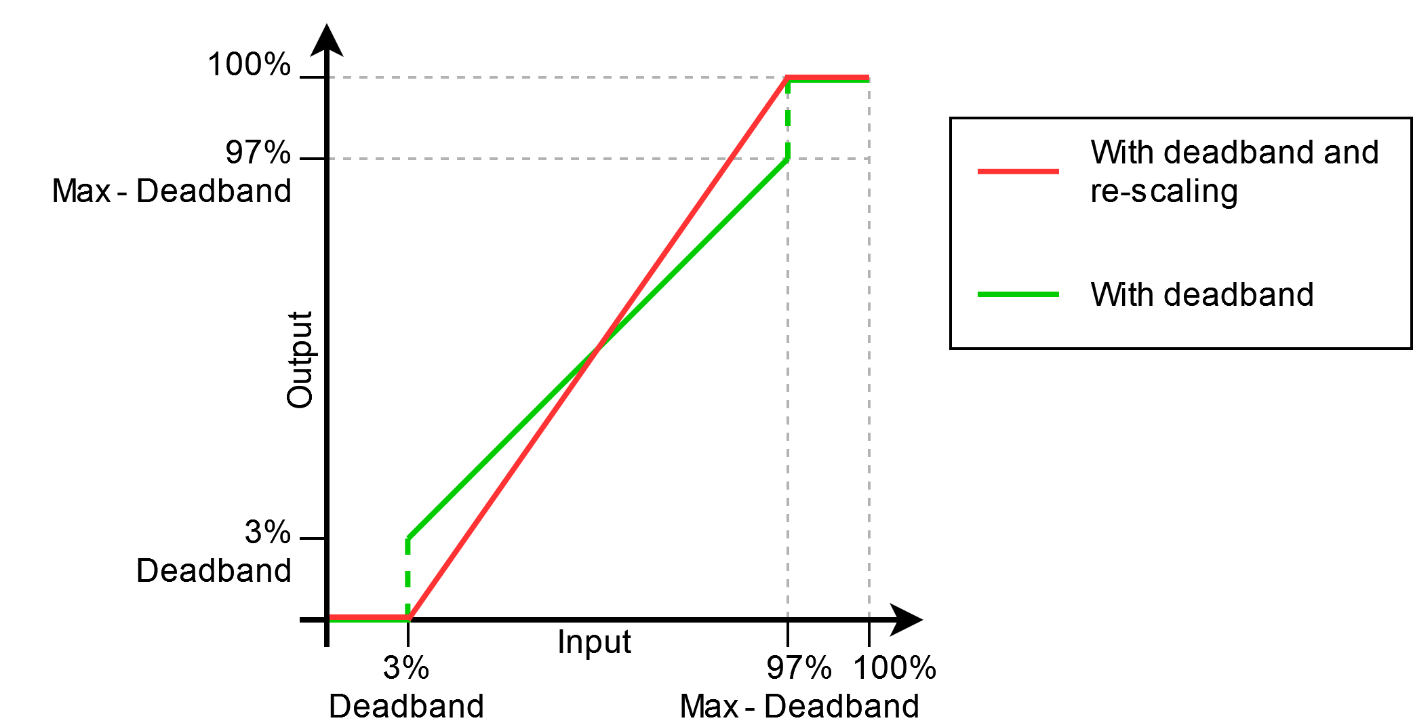
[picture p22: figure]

Then, all the in-between values, that are not affected by the deadband and range from 3% to 97% of THROTTLE_NORMALIZED, are scaled from 0 to THROTTLE_NORMALIZED, to eliminate the initial and final step.

Figure 3.6 Output of the deadband elaboration (green) and scaling (red).

#### Throttle Curve

After the deadband, we have a smooth, normalized throttle value. This value needs to be mapped to a output speed (duty cycle). The throttle curve is a function that takes as input a normalized throttle value (that ranges from 0 to THROTTLE_NORMALIZED) and returns a speed output expressed as duty cycle percentage (that ranges from 0% to 100%).

To be precise, the throttle curve returns a speed output that ranges from the min speed (SENSI parameter) to the max speed (LIMIT parameter)

The throttle curve is composed of two consecutive segments that intersect in a single point called vertex.

The vertex point coordinates are stored in the throttleCurveVertex variable in the following way:

- inputThrottle is the X coordinate of the vertex and is fixed by default at 50% of the throttle range (that is THROTTLE_NORMALIZED / 2). At this moment the user has no way to change this value
- curveSpeedDiff indicates how to calculate the Y coordinate of the vertex: this variable indicates the value of the Y coordinate as a percentage of the difference between the min and max speed (e.g., curveSpeedDiff = 50% means that the Y coordinate of the vertex is exactly the middle point between Min and Max speed). This implementation was chosen over an absolute value because it adapts automatically to changes in min and max speed. It is also more understandable from the user point of view. This variable corresponds to the CURVE parameter.

The Y coordinate of the vertex is calculated as:

y_V =MIN_(SPEED) +((MAX_(SPEED) - MIN_(SPEED) )*(CURVE)/100)

Where CURVE is a percentage which ranges from 10% to 90%.

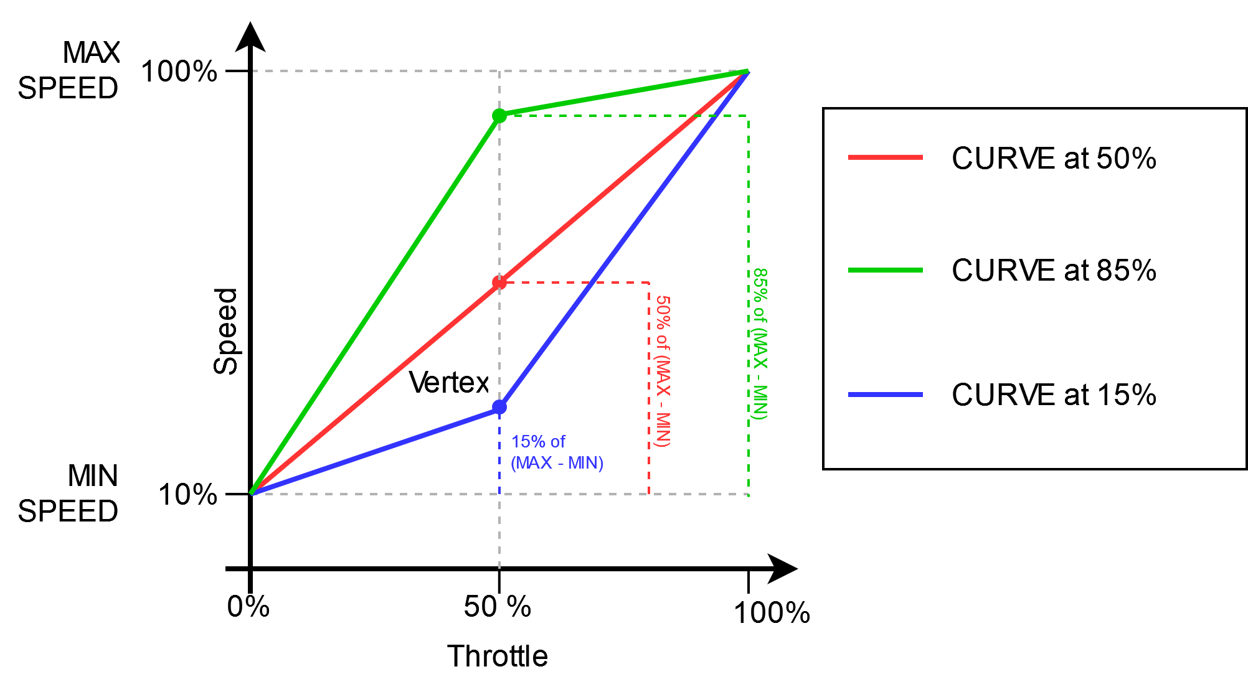
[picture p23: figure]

Once the coordinates of the throttle curve vertex are known ( x_V fixed at THROTTLE_NORMALIZED/2 and y_V calculated as shown above), the throttle curve is simply a function defined by cases

Figure 3.7 Example of throttle curve mapping with different CURVE values.

#### Antispin

The last passage of the throttle-to-speed pipeline is the antispin calculation. This passage applies the ANTIS parameter that limits the maximum increase in speed, in order to prevent the car from spinning due to a sudden acceleration.

The calculation takes into account the time between execution, the current requested speed and the output speed of the antispin calculation of the previous execution. The speed variables used in the calculation are multiplied by 1000, to increase the granularity.

Antispin is only applied during acceleration (when the current requested speed is higher than the previous output speed), while during deceleration the requested speed is not modified.

In this passage, the maximum possible speed increase between the current and previous execution is calculated as:

∆_(SPEED) = ((MAX_(SPEED) -MIN_(SPEED) )* ∆_t)/(ANTIS)

Where ∆_t is the time between executions, and ANTIS is the antispin parameter.

Then the output speed is calculated as

OUT_(SPEED) =min(PREV_(SPEED) + ∆_(SPEED) , REQ_(SPEED) )

Ensuring that the increase in speed is at most ∆_(SPEED) .

### Setting the PWM

At the end of the throttle-to-speed pipeline we have obtained a speed value that ranges from 0% to 100%. This speed value corresponds to the duty cycles of the PWM that controls the car motor.

In this last part of the Task 2 code, the PWM is set calling the HalfBridge_SetPwmDrag function, that takes as argument the duty cycle percentage and the drag percentage.

If the speed is 0%, then the output duty cycle will be 0%, and only the brake is applied (whose value corresponds to the BRAKE parameter).

If the speed is greater than 0%, than the speed value will be used as output duty cycle, and the value of the drag will be proportional to the trigger derivative, scaled from 0 to DRAGB.

In this case, only the negative derivative is used (when the trigger is being released).

#### Computing the trigger derivative

The trigger derivative is computer during the throttle-to-speed pipeline, and is calculated using the trigger value, after the normalization and the deadband elaboration.

A circular buffer that stores the latest 60 trigger values is used (that is, the amount of Task 2 executions that occur in the span of TRIG_AVG_TIME, 30 ms). At every execution, the current trigger value replaces the oldest value in the buffer.

The rolling average trigger value is calculated as the average of all the trigger values in the buffer, and the derivative is computer as the difference between the current trigger and the rolling average.

This operation returns a signed 16-bit integer value.

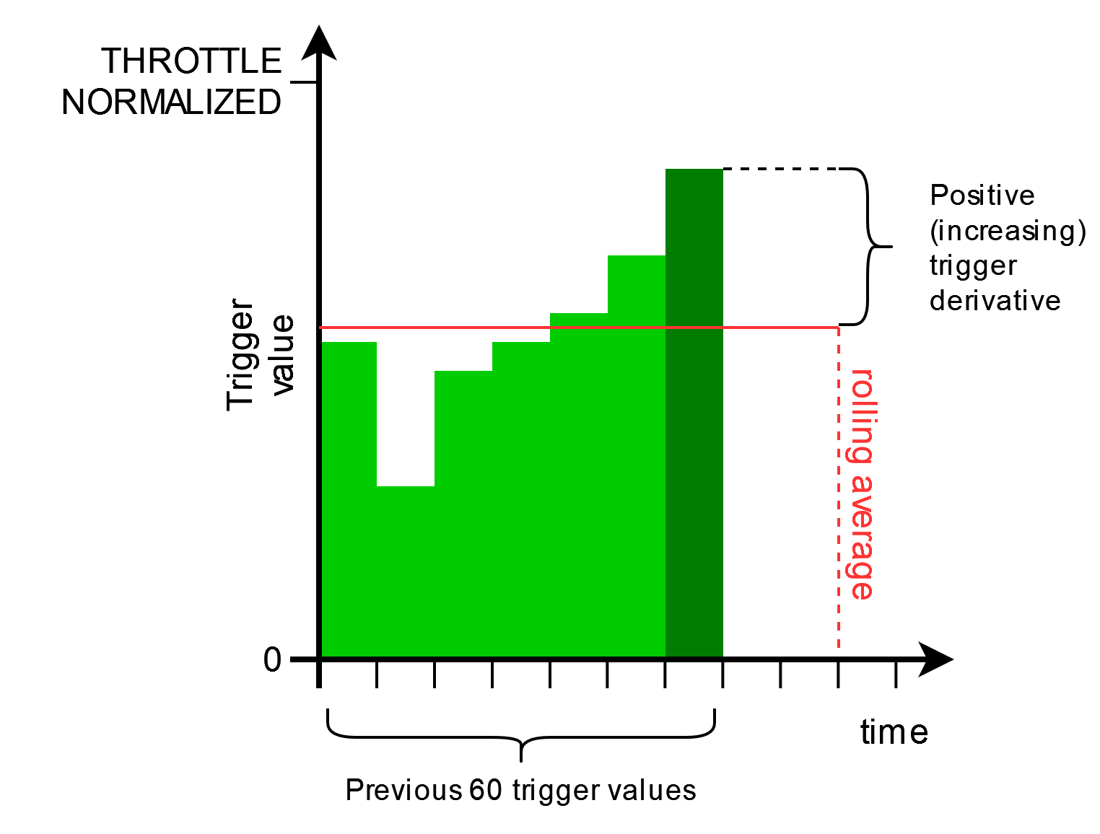
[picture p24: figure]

Figure 3.8 Example of trigger derivative calculation.

# 4 Revision History

Version | Date | Description
V1.0 | 15/10/2024 | Initial version

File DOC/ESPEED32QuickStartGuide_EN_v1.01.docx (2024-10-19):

# ESPEED32 Slot Car Electronic Speed Controller

Quick Start Guide

EN

## Introduction

The ESPEED32 is a powerful Slot Car Electronic Speed Controller based on the 32-bit ESP32 microcontroller.

## Calibration

The calibration of the trigger travel must be performed every time the trigger travel is changed, or the firmware is updated. To perform the trigger calibration, keep pressed the rotary selector while powering the ESPEED32, until the calibration screen appears. Fully press and release the trigger a few times, then press the rotary selector once. To verify a proper calibration, check if the throttle is showing 0% when the trigger is fully released, and 100% when the trigger is fully pressed.

## Navigating the screen

Rotate the rotary selector to scroll the settings in the main menu: the selected setting is highlighted. Press the selector once to change the value of the selected setting: the value is now highlighted. Rotate the selector to change the value of the selected setting, then press the selector again to confirm the value.

## Settings

SENSI – Sensitivity: Indicates the power provided to the motor when the minimum detectable pressure is applied to the trigger. The sensitivity should be at least sufficient for the car to start moving. If the track is “fast” or the car is “heavy”, then a higher sensitivity can be chosen. SENSI measurement unit is percent [%] and ranges from 0% to 90%.

BRAKE – Brake level: Indicates how strong the motor will brake when the trigger is completely released. In order to perform the brake, the motor is shorted with a PWM whose duty cycle is equal to the value of BRAKE. BRAKE measurement unit is percent [%] and ranges from 0% to 100% (100% means max brake is applied).

ANTIS – Anti-spin: Anti-spin (traction control) is used to provide a smooth power ramp to the motor, even if the trigger is pressed abruptly. ANTIS is expressed in milliseconds [ms]. It indicates how much time it takes for the motor to reach 100% power with the trigger fully pressed. If ANTIS is set to 150 ms and the trigger is pressed instantaneously, then the motor will receive a power ramp that will take 150ms to reach the max power. The higher the number the softer is the power ramp applied. ANTIS possible value ranges from 0 ms to 250 ms.

Typical ANTIS value: 130 ms for 1/32 cars; 0 ms for 1/24 cars

CURVE – Trigger-to-motor power curve: the CURVE parameter allows to customize the mapping of the trigger position to the motor power output. A default value of 50% corresponds to a linear curve. If CURVE is <50% the response of the trigger will be softer at the beginning of the travel and more aggressive at the end; vice versa if CURVE is >50%. Ranges from 10% to 90%.

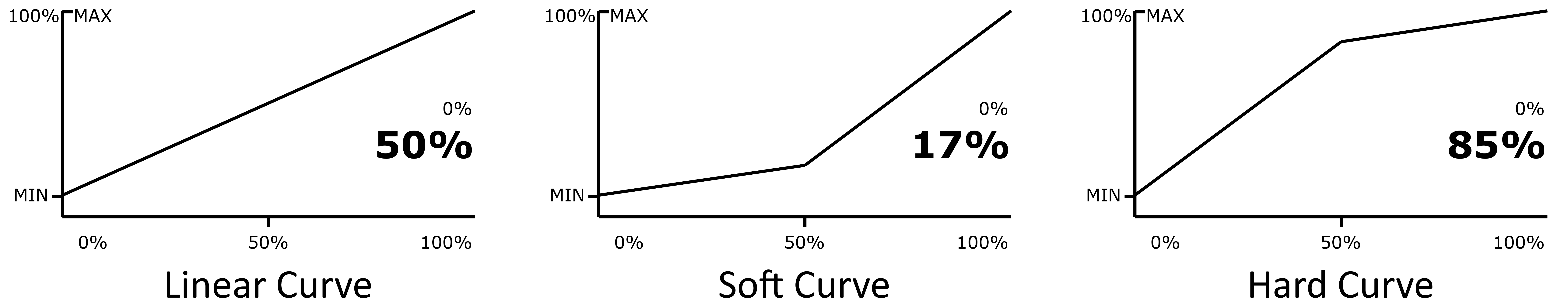
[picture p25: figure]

Figure 1 CURVE setting examples.

DRAGB – Drag Brake: applies some drag (soft brake) when the trigger is being released. The drag is applied only during the release movement of the trigger, so it’s very brief. DRAGB measurement unit is percent [%] and its value indicate the percentage of the trigger currently not being pushed to the motor that is converted to brake during the trigger release. Ranges from 0% to 100%. If DRAGB is > (100%-SENSI) then it will produce a different curve during the throttle release, to ensure up to 100% drag can be applied

PWM_F – motor PWM frequency: the frequency of the PWM (Pulse Width Modulation) used to control the motor. A higher frequency produces a softer response, especially at low trigger positions; a lower frequency produces higher torque with minimum throttle and more linear response. PWM_F measurements unit is Kilohertz [kHz] and ranges from 0.2kHz to 5.0kHz

Table 1 Settings overview

Setting | Recommended value | Range | | Unit
| | Min. | Max.
SENSI | 10 | 0 | 90 | %
BRAKE | 95 | 0 | 100 | %
ANTIS | 130 for 1/32 cars 0 for 1/24 cars | 0 | 250 | ms
CURVE | 50 | 10 | 90 | %
DRAGB | 100 | 0 | 100 | %
PWM_F | 3 | 0.2 | 5.0 | kHz

## Electrical Specifications - recommended operating condition

Setting | Symbol | Value | | | Unit
| | Min. | Typ. | Max.
Power supply voltage | VIN+ | 6.0 | 12 | 18 | V
Motor Current | I_(VDD) | 35 | 47 | 60 | mA
Startup Time | t_(startUp) | - | 150 | - | ms

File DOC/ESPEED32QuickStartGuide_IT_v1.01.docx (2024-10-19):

# ESPEED32 Quick Start Guide

Guida rapida

IT

## Introduzione

L’ ESPEED32 è un pulsante professionale per slot car basato sul microcontrollore ESP32 a 32 bit.

## Calibrazione

La calibrazione del grilletto deve essere eseguita ogni volta che si modifica la corsa del grilletto o si aggiorna il firmware. Per eseguire la calibrazione del grilletto, mantenere premuto il selettore rotativo mentre si alimenta l’ ESPEED32, finché non appare la schermata di calibrazione. A questo punto rilasciate il pulsante sul selettore rotativo. La calibrazione consiste nel premere e rilasciare completamente il grilletto 2-3 volte, quindi premere nuovamente volta il selettore rotativo per uscire e salvare la calibrazione. Per verificare che la calibrazione sia corretta, controllare se l’indicatore dell’acceleratore mostra 0% quando il grilletto è completamente rilasciato e 100% quando il grilletto è completamente premuto.

## Navigazione sullo schermo

Ruotare il selettore rotativo per scorrere le impostazioni nel menu principale: l'impostazione selezionata è evidenziata. Premere una volta il selettore per modificare il valore dell'impostazione selezionata: il valore è ora evidenziato. Ruotare il selettore per modificare il valore dell'impostazione selezionata, quindi premere nuovamente il selettore per confermare il valore.

## Impostazioni

SENSI – Sensibilità: Indica la potenza minima fornita al motore. E’ la potenza che viene applicata al motore alla minima pressione rilevabile al grilletto. La sensibilità dovrebbe essere almeno sufficiente per far partire l'auto. Se il percorso è "veloce" o l'auto è poco sensibile, è possibile scegliere una sensibilità (SENSI) maggiore, anche il 50% per esempio. L'unità di misura SENSI è percentuale [%] e varia da 0% a 90%.

BRAKE – Livello freno: Indica la potenza di frenata del motore quando il grilletto viene completamente rilasciato. Per eseguire la frenata, il motore viene messo in cortocircuito con un PWM il cui ciclo di lavoro è uguale al valore di BRAKE. L'unità di misura BRAKE è percentuale [%] e varia da 0% a 100% (100% significa che è applicata la massima frenata).

ANTIS – Antispin: Antispin (controllo della trazione)

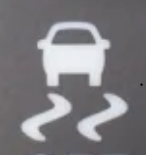
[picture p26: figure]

L’antispin viene utilizzato per fornire una rampa graduale di potenza al motore, anche se il grilletto viene premuto bruscamente. Questo previene lo slittamento della macchina. ANTIS è espresso in millisecondi [ms]. Indica quanto tempo impiega il motore a per andare da 0% al 100% di potenza quando il grilletto viene premulto bruscamente.Ad esempio, ANTIS= 150ms e il grilletto viene premuto istantaneamente, il motore riceverà una rampa di potenza che impiegherà 150 ms per raggiungere la potenza massima. Più alto è il numero sul parametero ANITS, più morbida è la rampa di potenza applicata. I valori possibili di ANTIS vanno da 0 ms a 250 ms. Valore ANTIS tipico: 130 ms per auto 1/32; 0 ms per auto 1/24


CURVE –Curva posizione trigger/potenza motore. il parametro CURVE consente di personalizzare la mappatura della posizione del trigger in base alla potenza in uscita dal motore. Un valore predefinito del 50% corrisponde a una curva lineare. Se CURVE è <50% la risposta del trigger sarà più morbida all'inizio della corsa e più aggressiva alla fine; viceversa seCURVE è >50%. Varia dal 10% al 90%.

DRAGB –Drag Brake: applica un leggero freno durante il rilascio del grilletto. La resistenza viene applicata solo durante il movimento di rilascio del grilletto, quindi l’effetto è molto breve ed è proporzionale alla velocità del rilascio. L’effetto è quello di sentire la frenata della macchina in anticipo rispetto al rilascio completo (inizia già dal rilascio del grilletto) quindi piu dolce ma piu efficatce perche. Essendo l’effetto delicato, è consigliato utilizzare valori alti (anche il 100%) per usurfruirne al meglio. L'unità di misura DRAGB è percentuale [%] e il suo valore indica la percentuale che viene convertita in freno durante il rilascio del grilletto. Varia da 0% a 100%. Se DRAGB è > (100%-SENSI) then it will produce a different curve during the throttle release, to ensure up to 100% drag can be applied.

PWM_F – frequenza PWM del motore: la frequenza del PWM (Pulse Width Modulation) utilizzato per controllare il motore. Una frequenza più alta produce una risposta più morbida, specialmente a basse posizioni di trigger; una frequenza più bassa produce una coppia più alta con accelerazione minima e una risposta più lineare. L'unità di misura PWM_F è Kilohertz [kHz] e varia da 0,2kHz a 5,0kHz

Parametro | Valore consigliato | Range | Unità di misura
SENSI | 10% | 0% - 90% | Percentuale [%]
BRAKE | 90% | 0% - 100% | Percentuale [%]
ANTIS | 130 ms per 1/32, 0 ms per 1/24 | 0 - 250 ms | Millisecondi [ms]
CURVE | 50% | 10% - 90% | Percentuale [%]
DRAGB | 100% | 0% - 100% | Percentuale [%]
PWM_F | 3 kHz | 0,2 - 5,0kHz | Chilohertz [kHz]

## Electrical Characteristics (recommended operating condition)

Setting | Symbol | Value | | | Unit
| | Min. | Typ. | Max.
Power supply voltage | VIN+ | 6.0 | 12 | 18 | V
Motor Current | I_(VDD) | 35 | 47 | 60 | mA
Startup Time | t_(startUp) | - | 150 | - | ms

ESPEED32|Quick Start Guide

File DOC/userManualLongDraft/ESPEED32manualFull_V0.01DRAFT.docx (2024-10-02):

# SlotEsp32 User Manual

The SlotEsp32 is an powerful Slot car controller based

Main features:

- Powerful ESP32 microcontroller: 1 core menu 1 core for trigger reading & motor control
- 40A protected Infineon automotive grade motor driver (no vintage fuses)
- Magnetic trigger Sensor with IC interface: accurate, no friction, no wear
- OLED display & Rotary Encoder open for upgrade
- Up to 10 model settings can be saved in the SlotEsp32 internal memory
- Open source firmware for endless parameter definitions
- Adjustable trigger travel and trigger tension

## Initial Calibration

## The SlotEsp32 has a magnetic trigger sensor and adjustable trigger travel, thereore the full pressed and full release trigger position has to be calibrated at first startup, or when the trigger travel is changed, or when the FW is updated.

To perform the trigger calibration keep the rotary encoder knob pressed while powering the SlotEsp32, then the calibration screen appears. Fully press and release the trigger 2-3 times, then press the trigger again. To verify a proper calibration, check if th throttle is showing 0% whn fully released and 100% when fully pressed.

## Store setting before removing the supply

## The

## SENSI – sensitivity (minimum speed)

Sensitivity, indicates the power provided to the motor when the trigger is pressed just at the minimum. The sensitivity should be at least sufficient for the car to start moving. If the track is “fast” or the car is “heavy” then a higher sensitivity can be chosen. Sensitivity measurement unit is percent [%].

Example of typical setting: SENSI = 20% for 1/32 cars, SENSI = 40% for 1/24 cars.

## BRAKE - brake level

Brake level, indicates how strong the car will brake when the throttle is completely released. In order to perform the brake, the motor is shorted with a PWM and a duty cycle equal to the brake %. 100% means that the brake is max.

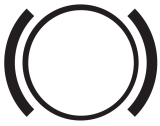
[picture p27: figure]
ISO 7000 - 1399, Brake system

Example starting point: 90% - 95% is a typical starting point

## ANTIS – antispin (traction control)

Antispin is used to provide a smooth power ramp to the motor, even if the throttle is pressed abruptly. Antispin is expressed in milliseconds [ms]. It indicates how much time it takes for the motor to reach 100% power. If the Antispin is set to 150 ms for instance, and the trigger is pressed instantaneously, then the motor will receive a power ramp, that will take 150ms to reach the max power. The higher the number the softer is the power ramp applied.

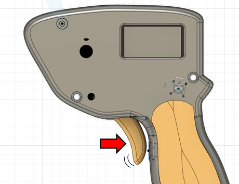
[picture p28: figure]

Example of typical setting: ANTIS = 130ms for 1/32 cars, ANTIS = 0 ms for 1/24 cars.

## CURVE – trigger position TO motor power curve

The curve sets how much power is provided to the motor based on the trigger position. Standard controllers has 50% curve (linear). If you set curve >50% the car is more aggressive, if you set <50% the trigger response is more soft with push only at the end of the trigger travel.

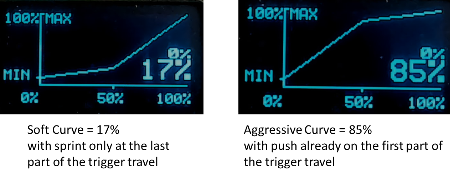
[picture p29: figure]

Example of typical setting: CURVE = 50% for most cars and pilots

## DRAGB – drag brake & anticipate brake

The Drag Brake applies some drag (soft brake) when the trigger is moving backward ( from pressed toward the brake position). So it anticipate the brake by reading the trigger movements. The drag is applied only during the release movement so it is very brief. Usually it is set to 100% so that all the % of throttle that is not pushed in to the motor , it is converted to brake during trigger release

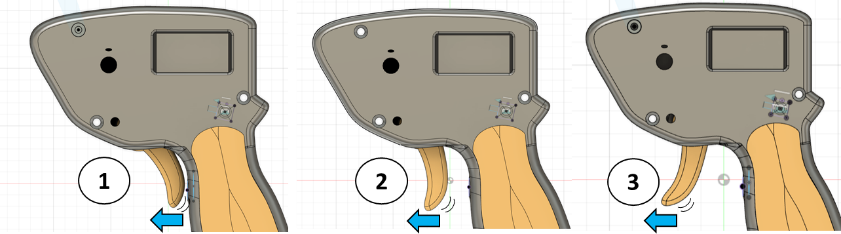
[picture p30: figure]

## PWM_F – motor PWM frequency

The Slotesp32, to control the motor speed uses a PWM (pulse width modulation). High PWM frequency (E.G. 4kHz) produces a softer response especially at low trigger positions. While a low PWM frequency (E.G. 1kHz) produces higher torque at minimum throttle and a more linear response (similar to a DC voltage).

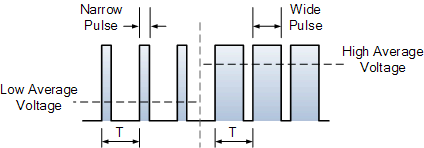
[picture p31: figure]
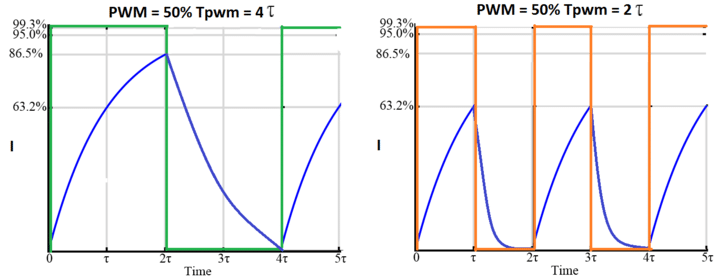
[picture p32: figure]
AB-022: PWM Frequency For Linear Motion Control - Precision Microdrives

Example of typical setting: PWM_F = 3kHz

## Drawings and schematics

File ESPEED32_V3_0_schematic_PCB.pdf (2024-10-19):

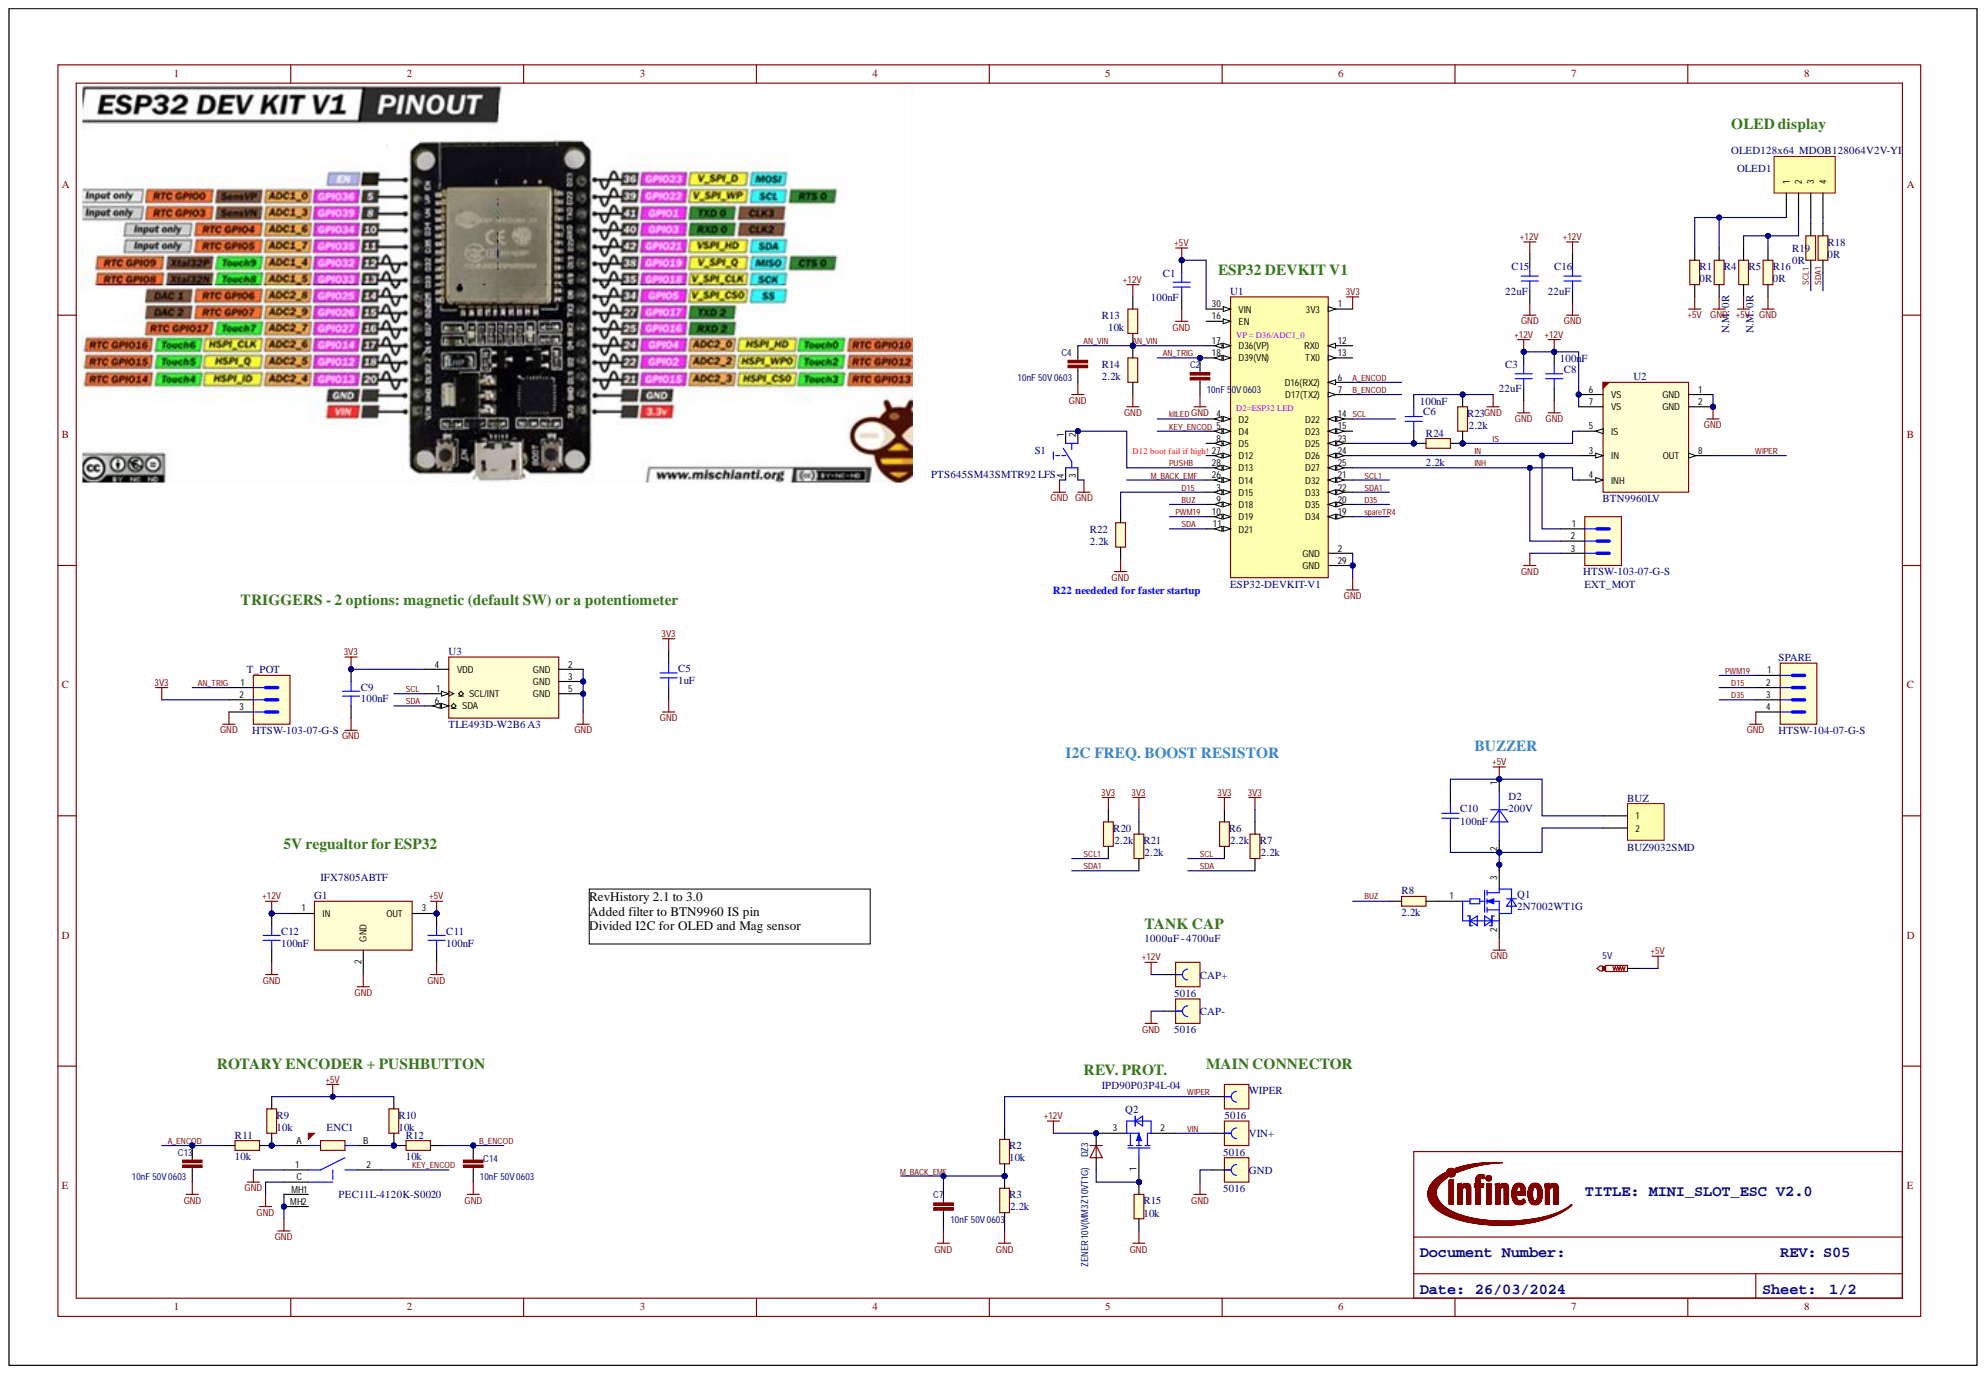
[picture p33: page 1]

Remarks: if not specified differently

D12 boot fail if high!

TRIGGERS - 2 options: magnetic (default SW) or a potentiometer

R22 neededed for faster startup

RevHistory 2.1 to 3.0
Added filter to BTN9960 IS pin
Divided I2C for OLED and Mag sensor

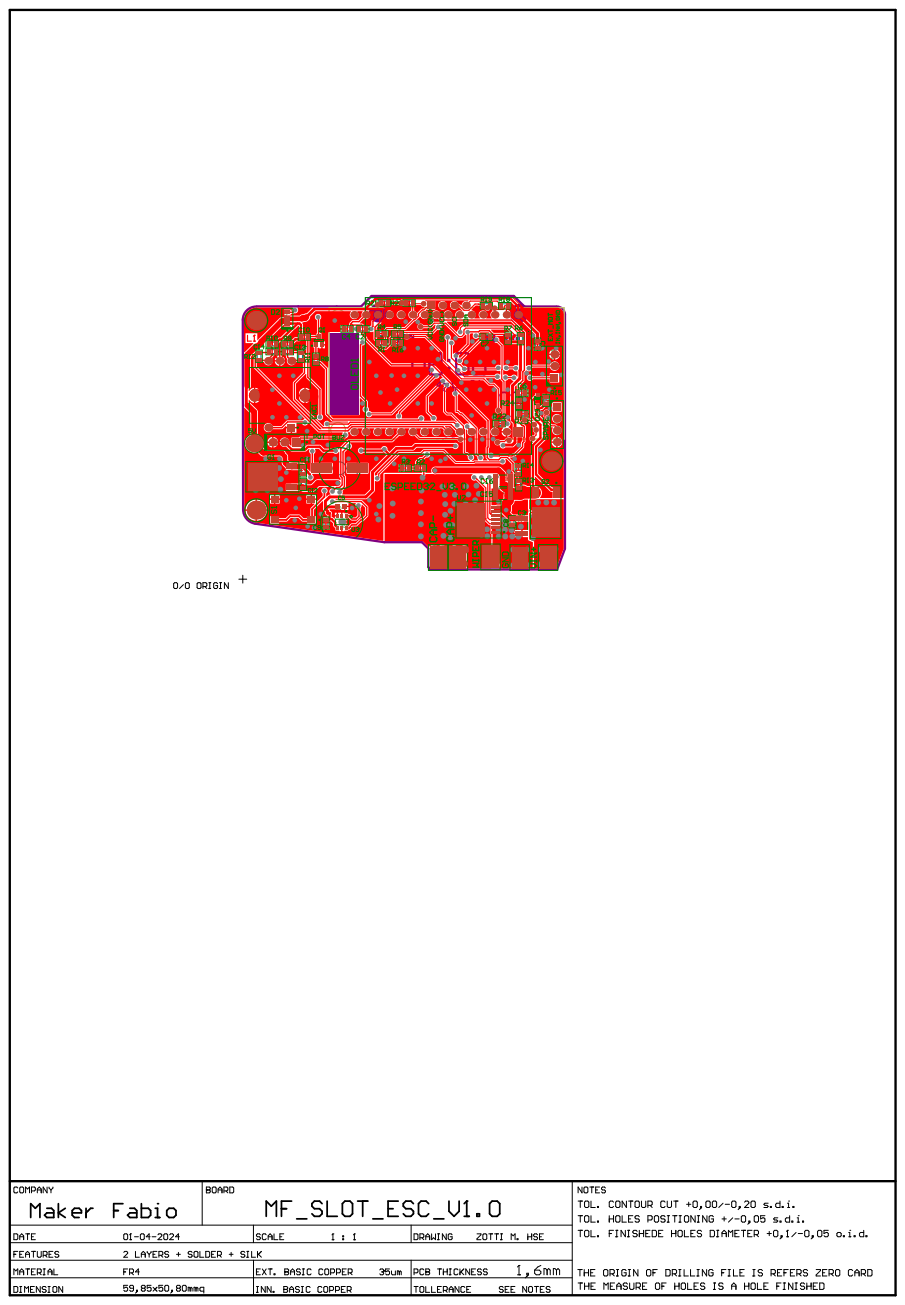
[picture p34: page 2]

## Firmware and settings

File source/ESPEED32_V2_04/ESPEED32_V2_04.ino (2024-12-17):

/*********************************************************************************************************************/
/*------------------------------------------------------Includes-----------------------------------------------------*/
/*********************************************************************************************************************/
#include "slot_ESC.h"

/*********************************************************************************************************************/
/*-------------------------------------------------------Macros------------------------------------------------------*/
/*********************************************************************************************************************/
#define BOOTLOADER_BUILD 1
//#define LOG_LOCAL_LEVEL ESP_LOG_NONE
#define CONFIG_BOOTLOADER_LOG_LEVEL ESP_LOG_NONE

#define SW_MAJOR_VERSION 2
#define SW_MINOR_VERSION 04
#define STORED_VAR_VERSION 2 /* tells which veriosn of stored variable is used for thisproject in case the stored var */
                             /* changes from previous SW release, please increase the STORED_VAR_VERSION by 1         */

/* Last modified: 17/10/2024 */
/*********************************************************************************************************************/
/*-------------------------------------------------Global variables--------------------------------------------------*/
/*********************************************************************************************************************/

TaskHandle_t Task1;
TaskHandle_t Task2;

static StateMachine_enum g_currState = INIT;
uint16_t debug;

/* Display Backbuffer */
#ifdef USE_BACKBUFFER
static uint8_t ucBackBuffer[1024];
#else
static uint8_t *ucBackBuffer = NULL;
#endif

OBDISP g_obd;       /* Display global instance */

char msgStr[50];    /* Display string global instance */


uint16_t g_carSel;  /* global variable telling whch car model has been selected */

/* Rotary Encoder global instance */
AiEsp32RotaryEncoder g_rotaryEncoder = AiEsp32RotaryEncoder(ENCODER_A_PIN, ENCODER_B_PIN, ENCODER_BUTTON_PIN, ENCODER_VCC_PIN, ENCODER_STEPS);

static uint8_t g_encoderMainSelector = 1;           /* Value of main menu selector (indicates selected item) */
static uint8_t g_encoderSecondarySelector = 0;      /* Value of secondarty selector (indicates selected item's value) */
static uint16_t *g_encoderSelectedValuePtr = NULL;  /* Global instance of pointer to the value selected by the encoder */


/* EEPROM stored values (mainly calibration) global instance */
StoredVar_type g_storedVar;

/* ESC internal variables gloabl instance */
ESC_type g_escVar{
  .outputSpeed_pct = 0,
  .trigger_raw = 0,
  .trigger_norm = 0,
  .triggerDerivative = 0,
  .encoderPos = 1,
  .Vin_mV = 0,
  .dualCurve = false
};

/* Main menu global instances */
Menu_type g_mainMenu{
  .lines = 3
};

/* Car menu global instances */
Menu_type g_carMenu{
  .lines = 3
};

/* Preferences global instance (for storing NVM data, replace EEPROM library) */
Preferences g_pref;

static uint32_t g_lastEncoderInteraction = 0;  /* tell how much time has passed since last time encoder whas rotated/pressed
                                                  so we can avoid keep printing the display menu and save CPU cycles */

/*********************************************************************************************************************/
/*--------------------------------------------- Function Declaration----------------------------------------*/
/*********************************************************************************************************************/
void IRAM_ATTR readEncoderISR();


/*********************************************************************************************************************/
/*---------------------------------------------Setup Function Implementations----------------------------------------*/
/*********************************************************************************************************************/

/* Setup */
void setup()
{

  /***** Pin and Serial Setup *****/
  HAL_PinSetup();

  /***** HalfBridge & HW Setup *****/
  HalfBridge_SetupFabio();

  /***** create a task that will be executed in the Task1code() and Task2code() funcitons, executed on core 0 and 1 *****/
  /* TASK1: slotESC state machine, managex OLED display and Encoder, low priority task */
  xTaskCreatePinnedToCore(
    Task1code, /* Task function. */
    "Task1",   /* name of task. */
    10000,     /* Stack size of task */
    NULL,      /* parameter of the task */
    1,         /* priority of the task */
    &Task1,    /* Task handle to keep track of created task */
    0);        /* pin task to core 0 */
  /* TASK2: perform trigger reading, trigger conditioning, PWM output */
  xTaskCreatePinnedToCore(
    Task2code, /* Task function. */
    "Task2",   /* name of task. */
    10000,     /* Stack size of task */
    NULL,      /* parameter of the task */
    2,         /* priority of the task */
    &Task2,    /* Task handle to keep track of created task */
    1);        /* pin task to core 1 */
}


/*********************************************************************************************************************/
/*---------------------------------------------MAIN LOOP IN TASKS----------------------------------------------*/
/*********************************************************************************************************************/

/**
 * Task 1: slotESC state machine: manage OLED display and Encoder, low priority task
 */
void Task1code(void *pvParameters) 
{
  for (;;) 
  {
    StateMachine_enum prevState = g_currState;  /* Keep track of the state at the previous loop */
    static uint16_t prevFreqPWM = 0;            /* Keep track if the PWM freq has changed */
    static MenuState_enum menuState = ITEM_SELECTION;   /* State of the Main Menu */
    static uint8_t swMajVer, swMinVer, storedVarVersion;/* SW major version, minor version,  storedVariable version stored in the eeprom */

    g_escVar.Vin_mV = HAL_ReadVoltageDivider(AN_VIN_DIV, RVIFBL, RVIFBH); /* Read VIN */

    if (g_currState != INIT) /* If the user params are already fetched from the EEPROM */
      {
        g_carSel = g_storedVar.selectedCarNumber;    /* Update global variable telling which car model is actually selected */
      }

    /* Task 1 state machine */
    switch (g_currState) {
      case INIT:

        g_pref.begin("stored_var", false); /* Open the "stored" namespace in read/write mode. If it doesn't exist, it creates it */
        
        if (g_pref.isKey("stored_var_ver") && g_pref.isKey("sw_maj_ver") && g_pref.isKey("sw_min_ver") && g_pref.isKey("user_param")) /* If all keys exists, then check their value */
        {
          /* Get the values of the sw version */
          swMajVer = g_pref.getUChar("sw_maj_ver");
          swMinVer = g_pref.getUChar("sw_min_ver");
          storedVarVersion = g_pref.getUChar("stored_var_ver");

          if ((storedVarVersion == STORED_VAR_VERSION) ) /* If the storedVariable version keys is equal to the STORED_VAR MACRO, then the stored param are already initialized woh the proper format*/
          {
            g_pref.getBytes("user_param", &g_storedVar, sizeof(g_storedVar)); /* Get the value of the stored user_param */
            initMenuItems();                                                  /* init menu items with EEPROM stored variables */

            /* If button is pressed at startup, go to CALIBRATION state */
            if (digitalRead(ENCODER_BUTTON_PIN) == BUTTON_PRESSED) 
            {
              g_currState = CALIBRATION;      /* Go to CALIBRATION state */
              /* Reset Min and Max to the opposite side, in order to have effective calibration */
              g_storedVar.minTrigger_raw = MAX_INT16;
              g_storedVar.maxTrigger_raw = MIN_INT16;
              calibSound();             /* Play calibration sound */
              initDisplayAndEncoder();  /* init and clear OLED and Encoder */

              /* Wait until button is released, then go to CALIBRATION state */
              while (digitalRead(ENCODER_BUTTON_PIN) == BUTTON_PRESSED)
              {
                showScreenPreCalibration();
              }
              
              obdFill(&g_obd, OBD_WHITE, 1); /* Clear OLED */
            }
            else  /* If button is NOT pressed at startup, go to RUNNING state */
            {
              g_currState = WELCOME;                    /* Go to WELCOME state */
              g_carSel = g_storedVar.selectedCarNumber; /* now it is safe to address the proper car */
              initDisplayAndEncoder();  /* init and clear OLED and Encoder */
              onSound();                /* Play ON sound */
            }

            g_pref.end(); /* Close the namespace */
            break;        /* Break the switch case: if code reaches here, it means that the stored user param and sw versions are OK */
          }
        }

        /* If the code reaches here it means that:
        - the sw version keys are not present --> stored var are not initialized
        - the sw version stored are not up to date --> stored var are initialized but might be outdated

        Calibration values are NOT stored, go to CALIBRATION state */
        initDisplayAndEncoder();  /* init and clear OLED and Encoder */
                              
        g_pref.clear();           /* Clear all the keys in this namespace */
        

        /* Store the correct SW version */
        g_pref.putUChar("sw_maj_ver", SW_MAJOR_VERSION);
        g_pref.putUChar("sw_min_ver", SW_MINOR_VERSION);
        
        g_pref.putUChar("stored_var_ver", STORED_VAR_VERSION);

        initStoredVariables();  /* Initialize stored variables with default values */

        /* Reset Min and Max to the opposite side, in order to have effective calibration */
        g_storedVar.minTrigger_raw = MAX_INT16;
        g_storedVar.maxTrigger_raw = MIN_INT16;
        calibSound();                   /* Play calibration sound */
        g_currState = CALIBRATION;      /* Go to CALIBRATION state */
        obdFill(&g_obd, OBD_WHITE, 1); /* Clear OLED */
        /* Press and release button to go to CALIBRATION state */
        while (!g_rotaryEncoder.isEncoderButtonClicked()) /* Loop until button is pressed */
        {
          showScreenNoEEPROM();
        }

        break;


      case CALIBRATION:
        /* Read Throttle */
        throttleCalibration(g_escVar.trigger_raw);    /* trigger raw is continuously read on task2 */
        showScreenCalibration(g_escVar.trigger_raw);  /* Show calibration screen */
        /* Exit calibration if button is presseded */
        if (g_rotaryEncoder.isEncoderButtonClicked())  /* exit calibration and save calibration data to EEPROM */
        {
          offSound();
          initMenuItems();  /* Init Menu Items */
          g_pref.putBytes("user_param", &g_storedVar, sizeof(g_storedVar)); /* Put the value of the stored user_param */
          g_pref.end();                                                     /* Close the namespace */
          HalfBridge_Enable();    /* Enable HalfBridge */
          g_currState = WELCOME;  /* Go to WELCOME state */
        }
        break;


      case WELCOME:
        /* This WELCOME state is only used to show the SW versions on the Screen, but the controller is actually fully operational:
            - Calibration is OKAY (either just done, or using stored values)
            - User param are OKAY (either just initialized to default, or using stored values)
            - Trigger is being read on Task 2

          The user trigger input is being elaborated and the correct speed (PWM) output is being produced for the whole duration of the WELCOME state */

        showScreenWelcome();    /* Show welcome screen */
        delay(1000);            /* Wait one second */
        g_currState = RUNNING;  /* Go to RUNNING state */
        break;


      case RUNNING: /* when the global variable State is in RUNNING the Task2 will elaborate the trigger to produce the PWM out */

        /* Change menu state if encoder button is clicked */
        if (g_rotaryEncoder.isEncoderButtonClicked()) 
        {
          menuState = rotary_onButtonClick(menuState);  /* This function is called if the encoder is pressed
                                                           Take the current menu state and returns the next menu state */
          g_lastEncoderInteraction = millis();          /* Update last encoder interaction */
        }

        /* Get encoder position if it was changed*/
        if (g_rotaryEncoder.encoderChanged()) 
        {
          g_escVar.encoderPos = g_rotaryEncoder.readEncoder();  /* Update the global ESC variable keeping track of the encoder value (position) */
          g_lastEncoderInteraction = millis();  /* Update last encoder interaction */
        }

        /* Change Encoder variable depending on menu state */
        if (menuState == ITEM_SELECTION) 
        {
          g_encoderMainSelector = g_escVar.encoderPos;  /* If in ITEM_SELECTION, update the encoder MainSelector with the encoder position */
        }
        if (menuState == VALUE_SELECTION) 
        {
          g_encoderSecondarySelector = g_escVar.encoderPos;         /* If in ITEM_SELECTION, update the encoder SecondaryEncoder with the encoder position */
          *g_encoderSelectedValuePtr = g_encoderSecondarySelector;  /* Also update the value of the selected parameter */
          //g_storedVar.carParam[g_carSel].throttleCurveVertex.curveSpeedDiff = saturateParamValue(g_storedVar.carParam[g_carSel].throttleCurveVertex.curveSpeedDiff, THROTTLE_CURVE_SPEED_DIFF_MIN_VALUE, THROTTLE_CURVE_SPEED_DIFF_MAX_VALUE); /* Regulate min value for throttle setpoint */
        }
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
void loop() {}

/*********************************************************************************************************************/
/*---------------------------------------------Setup Function Implementations----------------------------------------------*/
/*********************************************************************************************************************/

/*
  Initialize OLED display and encoder.
  This is done separately from the HW init to shorten the startup time.
*/
void initDisplayAndEncoder() 
{
  uint16_t rc;
  /***** OLED Display Setup *****/
  rc = obdI2CInit(&g_obd, MY_OLED, OLED_ADDR, FLIP180, INVERT_DISP, USE_HW_I2C, SDA1_PIN, SCL1_PIN, RESET_PIN, 800000L);  // use standard I2C bus at 400Khz
  if (rc != OLED_NOT_FOUND) 
  {
    obdSetBackBuffer(&g_obd, ucBackBuffer);
    obdFill(&g_obd, OBD_WHITE, 1);
  } 
  else 
  {
    Serial.println("Error! Failed OLED Display initialization!");
  }

  /***** Encoder Setup *****/
  g_rotaryEncoder.begin();
  g_rotaryEncoder.setup(readEncoderISR);
  g_rotaryEncoder.setBoundaries(1, MENU_ITEMS_COUNT, false); /* minValue, maxValue, circleValues true|false (when max go to min and vice versa) */
  g_rotaryEncoder.setAcceleration(MENU_ACCELERATION);        /* Larger number = more accelearation; 0 or 1 means disabled acceleration */
}


/* Rotary Encoder ISR */
void IRAM_ATTR readEncoderISR() {
  g_rotaryEncoder.readEncoder_ISR();
}


/**
 * Initialize the stored variables with default values.
   This is done for every CAR in the CarParam array.
 */
void initStoredVariables() {
  for (int i = 0; i < CAR_MAX_COUNT; i++) {
    g_storedVar.carParam[i].minSpeed = MIN_SPEED_DEFAULT;
    g_storedVar.carParam[i].brake = BRAKE_DEFAULT;
    g_storedVar.carParam[i].dragBrake = DRAG_BRAKE_DEFAULT;
    g_storedVar.carParam[i].maxSpeed = MAX_SPEED_DEFAULT;
    g_storedVar.carParam[i].throttleCurveVertex = { THROTTLE_CURVE_INPUT_THROTTLE_DEFAULT, THROTTLE_CURVE_SPEED_DIFF_DEFAULT };
    g_storedVar.carParam[i].antiSpin = ANTISPIN_DEFAULT;
    g_storedVar.carParam[i].freqPWM = PWM_FREQ_DEFAULT;
    g_storedVar.carParam[i].carNumber = i;
    sprintf(g_storedVar.carParam[i].carName, "CAR%1d", i);
  }
  g_storedVar.selectedCarNumber = 0;
  g_storedVar.minTrigger_raw = 0;
  g_storedVar.maxTrigger_raw = ACD_RESOLUTION_STEPS;
}


/**
 * Initialize the menu items with the value from the stored variables.
   Insert the items one by one in the main menu global instance.
   Then insert the items (cars) in the car menu.
   To add an item:
    - update the value of MENU_ITEMS_COUNT to match the amount of items in the menu.
    - update MAX_ITEMS so that it is greater or equal MENU_ITEMS_COUNT.
    - Add the item here, in the desired position (check the comment in slot_ESC.h MenuItem_type to know more).
 */
void initMenuItems() {
  int i = 0;
  /* Init menu items */
  sprintf(g_mainMenu.item[i].name, "SENSI");
  g_mainMenu.item[i].value = (void *)&g_storedVar.carParam[g_carSel].minSpeed;
  g_mainMenu.item[i].type = VALUE_TYPE_INTEGER;
  g_mainMenu.item[i].unit = '%';
  g_mainMenu.item[i].maxValue = min(MIN_SPEED_MAX_VALUE, (int)g_storedVar.carParam[g_carSel].maxSpeed);
  g_mainMenu.item[i].minValue = 0;
  g_mainMenu.item[i].callback = ITEM_NO_CALLBACK;

  sprintf(g_mainMenu.item[++i].name, "BRAKE");
  g_mainMenu.item[i].value = (void *)&g_storedVar.carParam[g_carSel].brake;
  g_mainMenu.item[i].type = VALUE_TYPE_INTEGER;
  g_mainMenu.item[i].unit = '%';
  g_mainMenu.item[i].maxValue = BRAKE_MAX_VALUE;
  g_mainMenu.item[i].minValue = 0;
  g_mainMenu.item[i].callback = ITEM_NO_CALLBACK;

  sprintf(g_mainMenu.item[++i].name, "ANTIS");
  g_mainMenu.item[i].value = (void *)&g_storedVar.carParam[g_carSel].antiSpin;
  g_mainMenu.item[i].type = VALUE_TYPE_INTEGER;
  g_mainMenu.item[i].unit = 'm';
  g_mainMenu.item[i].maxValue = ANTISPIN_MAX_VALUE;
  g_mainMenu.item[i].minValue = 0;
  g_mainMenu.item[i].callback = ITEM_NO_CALLBACK;

  sprintf(g_mainMenu.item[++i].name, "CURVE");
  g_mainMenu.item[i].value = (void *)&g_storedVar.carParam[g_carSel].throttleCurveVertex.curveSpeedDiff;
  g_mainMenu.item[i].type = VALUE_TYPE_INTEGER;
  g_mainMenu.item[i].unit = '%';
  g_mainMenu.item[i].maxValue = THROTTLE_CURVE_SPEED_DIFF_MAX_VALUE;
  g_mainMenu.item[i].minValue = THROTTLE_CURVE_SPEED_DIFF_MIN_VALUE;
  g_mainMenu.item[i].callback = &showCurveSelection;

  sprintf(g_mainMenu.item[++i].name, "DRAGB");
  g_mainMenu.item[i].value = (void *)&g_storedVar.carParam[g_carSel].dragBrake;
  g_mainMenu.item[i].type = VALUE_TYPE_INTEGER;
  g_mainMenu.item[i].unit = '%';
  g_mainMenu.item[i].maxValue = DRAG_MAX_VALUE;
  g_mainMenu.item[i].minValue = 0;
  g_mainMenu.item[i].callback = ITEM_NO_CALLBACK;

  sprintf(g_mainMenu.item[++i].name, "PWM_F");
  g_mainMenu.item[i].value = (void *)&g_storedVar.carParam[g_carSel].freqPWM;
  g_mainMenu.item[i].type = VALUE_TYPE_DECIMAL;
  g_mainMenu.item[i].unit = 'k';
  g_mainMenu.item[i].maxValue = FREQ_MAX_VALUE / 100;
  g_mainMenu.item[i].minValue = FREQ_MIN_VALUE / 100;
  g_mainMenu.item[i].decimalPoint = 1;
  g_mainMenu.item[i].callback = ITEM_NO_CALLBACK;

  sprintf(g_mainMenu.item[++i].name, "LIMIT");
  g_mainMenu.item[i].value = (void *)&g_storedVar.carParam[g_carSel].maxSpeed;
  g_mainMenu.item[i].type = VALUE_TYPE_INTEGER;
  g_mainMenu.item[i].unit = '%';
  g_mainMenu.item[i].maxValue = MAX_SPEED_DEFAULT;
  g_mainMenu.item[i].minValue = max(5, (int)g_storedVar.carParam[g_carSel].minSpeed + 5);
  g_mainMenu.item[i].callback = ITEM_NO_CALLBACK;

  sprintf(g_mainMenu.item[++i].name, "*CAR*");
  g_mainMenu.item[i].value = (void *)&g_storedVar.carParam[g_carSel].carName;
  g_mainMenu.item[i].type = VALUE_TYPE_STRING;
  g_mainMenu.item[i].maxValue = CAR_MAX_COUNT - 1;  // so menu will scroll in the array (CAR_MAX_COUNT long)
  g_mainMenu.item[i].minValue = 0;
  g_mainMenu.item[i].callback = &showSelectRenameCar;

  /* Init Car selection menu items */
  for (uint8_t j = 0; j < CAR_MAX_COUNT; j++)
  {
    sprintf(g_carMenu.item[j].name, (const char *)g_storedVar.carParam[j].carName);
    g_carMenu.item[j].value = (void *)&g_storedVar.carParam[j].carNumber;
  }
}


/**
 * Show the Welcome screen
 */
void showScreenWelcome() 
{
  obdWriteString(&g_obd, 0, 16, 12, (char *)"ESPEED32", FONT_12x16, OBD_BLACK, 1);
  sprintf(msgStr, "V%d.%02d", SW_MAJOR_VERSION, SW_MINOR_VERSION);  
  obdWriteString(&g_obd, 0, 34, 28, msgStr, FONT_12x16, OBD_WHITE, 1);
}


/**
 * Show the Pre-Calibration screen, when the button is pressed during startup, but not yet released
 */
void showScreenPreCalibration() 
{
  sprintf(msgStr, "ESPEED32 v%d.%02d", SW_MAJOR_VERSION, SW_MINOR_VERSION);  //print SW version
  obdWriteString(&g_obd, 0, 8, 0, msgStr, FONT_8x8, OBD_BLACK, 1);
  obdWriteString(&g_obd, 0, (OLED_WIDTH / 2) - 48, 1 * HEIGHT8x8, (char *)"Release button", FONT_8x8, OBD_BLACK, 1);
  obdWriteString(&g_obd, 0, (OLED_WIDTH / 2) - 48, 2 * HEIGHT8x8, (char *)"to calibrate", FONT_8x8, OBD_BLACK, 1);
  obdWriteString(&g_obd, 0, (OLED_WIDTH / 2) - 48, 3 * HEIGHT8x8, (char *)"     OR    ", FONT_8x8, OBD_BLACK, 1);
  obdWriteString(&g_obd, 0, (OLED_WIDTH / 2) - 48, 4 * HEIGHT8x8, (char *)"remove power", FONT_8x8, OBD_BLACK, 1);
  obdWriteString(&g_obd, 0, (OLED_WIDTH / 2) - 48, 5 * HEIGHT8x8, (char *)"  to exit  ", FONT_8x8, OBD_BLACK, 1);
}


/**
 * Show the screen indicating that the stored variables are not present in the EEPROM
 */
void showScreenNoEEPROM() 
{
  sprintf(msgStr, "ESPEED32 v%d.%02d", SW_MAJOR_VERSION, SW_MINOR_VERSION);  //print SW version
  obdWriteString(&g_obd, 0, 0, 0, msgStr, FONT_8x8, OBD_WHITE, 1);
  obdWriteString(&g_obd, 0, (OLED_WIDTH / 2) - 64, 3 * HEIGHT8x8, (char *)"EEPROM NOT init!", FONT_8x8, OBD_BLACK, 1);
  obdWriteString(&g_obd, 0, (OLED_WIDTH / 2) - 48, 5 * HEIGHT8x8, (char *)"Press button", FONT_8x8, OBD_BLACK, 1);
  obdWriteString(&g_obd, 0, (OLED_WIDTH / 2) - 48, 6 * HEIGHT8x8, (char *)"to calibrate", FONT_8x8, OBD_BLACK, 1);
}
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

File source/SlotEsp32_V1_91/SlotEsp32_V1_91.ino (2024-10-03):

/*********************************************************************************************************************/
/*------------------------------------------------------Includes-----------------------------------------------------*/
/*********************************************************************************************************************/
#include "slot_ESC.h"

/*********************************************************************************************************************/
/*-------------------------------------------------------Macros------------------------------------------------------*/
/*********************************************************************************************************************/
#define SW_MAJOR_VERSION 1
#define SW_MINOR_VERSION 91
/* Last modified: 01/10/2024 */
/*********************************************************************************************************************/
/*-------------------------------------------------Global variables--------------------------------------------------*/
/*********************************************************************************************************************/

TaskHandle_t Task1;
TaskHandle_t Task2;

static FSM_state_enum currState = SELF_CHECK;
uint16_t debug;

/* Display Backbuffer */
#ifdef USE_BACKBUFFER
static uint8_t ucBackBuffer[1024];
#else
static uint8_t *ucBackBuffer = NULL;
#endif

/* Display global instance */
OBDISP obd;

/* Display string global instance */
char msgStr[50];

uint16_t gCarSel;  // global variable telling whch car model has been selected

/* Rotary Encoder global instance */
AiEsp32RotaryEncoder rotaryEncoder = AiEsp32RotaryEncoder(ENCODER_A_PIN, ENCODER_B_PIN, ENCODER_BUTTON_PIN, ENCODER_VCC_PIN, ENCODER_STEPS);

/* Value of main menu selector (indicates selected item) */
static uint8_t encoderMainSelector = 1;
/* Value of secondarty selector (indicates selected item's value) */
static uint8_t encoderSecondarySelector = 0;
/* Global instance of pointer to the value selected by the encoder */
static uint16_t *encoderSelectedValuePtr = NULL;

/* EEPROM stored values (mainly calibration) global instance */
EEPROM_stored_var_type storedVar;

/* ESC internal variables gloabl instance */
ESC_var_type escVar{
  .outSpdSetPerc  = 0,     // [%] set speed
  .trigRaw    = 0,
  .trigNorm   = 0,  //  Normalized trigger position
  .trigDeriv  = 0,
  .encoderPos = 1,    // [%] encodReadRaw
  .Vin_mV = 0
};

/* Menu global instances */
menu_type mainMenu{
  .lines = 3
};

menu_type carMenu{
  .lines = 3
};

static uint32_t lastEncoderInteraction = 0; // tell how long is the encoder untouched, so can avoid keep printing he display menu and save CPU cycles

String dragBrakeTypes[] = {" FULL", " DECE"};   /* Names of two types of dragBrake */ 
/*********************************************************************************************************************/
/*--------------------------------------------- Function Declaration----------------------------------------*/
/*********************************************************************************************************************/
void IRAM_ATTR readEncoderISR();


/*********************************************************************************************************************/
/*---------------------------------------------Setup Function Implementations----------------------------------------*/
/*********************************************************************************************************************/

/* Setup */
void setup() {

  /***** Pin and Serial Setup *****/
  HAL_PinSetup();

  /***** OLED Display Setup *****/
  int rc = obdI2CInit(&obd, MY_OLED, OLED_ADDR, FLIP180, INVERT_DISP, USE_HW_I2C, SDA1_PIN, SCL1_PIN, RESET_PIN, 800000L);  // use standard I2C bus at 400Khz
  if (rc != OLED_NOT_FOUND) {
    obdSetBackBuffer(&obd, ucBackBuffer);
    obdFill(&obd, OBD_WHITE, 1);
  } else {
    Serial.println("Error! Failed OLED Display initialization!");
  }

  /***** HalfBridge & HW Setup *****/
  HalfBridge_Setup();

  /***** Encoder Setup *****/
  rotaryEncoder.begin();
  rotaryEncoder.setup(readEncoderISR);
  rotaryEncoder.setBoundaries(1, MENU_ITEMS_COUNT, false); /* minValue, maxValue, circleValues true|false (when max go to min and vice versa) */
  rotaryEncoder.setAcceleration(MENU_ACCELERATION);        /* Larger number = more accelearation; 0 or 1 means disabled acceleration */

  /***** create a task that will be executed in the Task1code() and Task2code() funcitons, executed on core 0 and 1 *****/ 
  /* Task1code:slotESC state machine, managex OLED display and Encoder, low priority task */
  xTaskCreatePinnedToCore(
                    Task1code,   /* Task function. */
                    "Task1",     /* name of task. */
                    10000,       /* Stack size of task */
                    NULL,        /* parameter of the task */
                    1,           /* priority of the task */
                    &Task1,      /* Task handle to keep track of created task */
                    0);          /* pin task to core 0 */        
  /* TASK2 : perform trigger reading, trigger conditioning, PWM output */          
  xTaskCreatePinnedToCore(
                    Task2code,   /* Task function. */
                    "Task2",     /* name of task. */
                    10000,       /* Stack size of task */
                    NULL,        /* parameter of the task */
                    2,           /* priority of the task */
                    &Task2,      /* Task handle to keep track of created task */
                    1);          /* pin task to core 1 */
}


/*********************************************************************************************************************/
/*---------------------------------------------MAIN LOOP IN TASKS----------------------------------------------*/
/*********************************************************************************************************************/
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

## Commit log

2024-10-03 Fix: staying in the CURVE screen no longer causes the ESP32 to crash. The crash was due to the watchdog not being reset, fixed by calling vTaskDelay(10) at the end of each loop
    [SlotEsp32_V1_91.ino]
2024-10-19 Reorganized folders
    produced new BOM and output files for HW version 3
    [ESPEED32_V03.SchDoc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]
2024-10-19 Updated BOM version number
    [BOM_Assembly_MiniSlotESC_V3.0draft.xlsx]
2024-10-19 updated Gerber, BOM and Pick and place
    [BOM_ESPEED32_V3_0_JLCPCB_only.xlsx, BOM_ESPEED32_V3_0_complete.xlsx, ESPEED32_V3_0.PrjPcb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]
2024-10-19 added pdf SCH and layout at the main root
    [ESPEED32_V03.SchDoc]
2024-10-19 updated rev history on SCH V3.0
    [ESPEED32_V3_0.PrjPcb]
2024-11-19 Update README.md
    added warning on the magnetic sensor delivery date
2024-11-20 tle493d w2B6A0 sensor config
2024-11-23 REmoved some old versions
    V2:11 Antispin stats from ANTISPIN_PERC_START instead of min speed, in order to rise the current earlier and have a more flat current during the ramp
    V2:08 Fixed negative derivate at 0 speed, this was impacting initial speed using antispin and producing random 90% duty glitches at startup or very low duty due to dual curve
    [5Washer5slides1trig.3mf, Body1.3mf, HandleBot_V20.3mf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]
2024-12-16 cleaned folders
    [BOM_Assembly_MiniSlotESC_V3.0draft.xlsx, HandleBotTextV37.3mf, HandleTopTextV39.3mf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]
